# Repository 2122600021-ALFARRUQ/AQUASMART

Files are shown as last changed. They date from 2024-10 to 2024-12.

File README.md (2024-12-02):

flyer

# AQUA SMART
<div align="center">
    AQUA SMART Logo
</div>

## **Supported By:**  
🌟 **Dosen Pengampu:** Akhmad Hendriawan, S.T., M.T.  *(NIP: 197501272002121003)*  
🎓 **Mata Kuliah:** IOT dan Jaringan Sensor  
🎯 **Program Studi:** Sarjana Terapan Teknik Elektronika  
🏫 **Politeknik Elektronika Negeri Surabaya**  

# Daftar Isi

- [Deskripsi](#deskripsi)
- [Buku Panduan](#buku-panduan)
- [Komponen](#komponen)
   * [1. ESP32](#1-esp32)
   * [2. Sensor Ultrasonic](#2-sensor-ultrasonic)
   * [3. Flow Sensor](#3-flow-sensor)
   * [4. Adaptor 12V 2A](#4-adaptor-12v-2a)
   * [5. Solenoid Valve](#5-solenoid-valve)
   * [6. Modul Relay](#6-modul-relay)
- [Diagram Arsitektur](#diagram-arsitektur)
- [Tim Pengembang](#tim-pengembang)
- [Timeline Pengembangan](#timeline-pengembangan)
- [Rincian Pengeluaran Biaya](#rincian-pengeluaran-biaya)
- [Hardware](#hardware)
  * [1. Schematic Rangkaian](#1-schematic-rangkaian)
  * [2. Desain PCB](#2-desain-pcb)
  * [3. 3D Model PCB](#3-3d-model-pcb)
  * [4. Hasil 3D](4-hasil-3d)
- [Software](#software)
  * [1. Flowchart](#1-flowchart)
  * [2. Simulasi Wokwi](#2-simulasi-wokwi)
  * [3. Node-Red](#3-node-red)
  * [4. Sequence Diagram](#4-sequence-diagram)
  * [5. Class Diagram](#5-class-diagram)
- [Web APP](#web-app)
- [Dokumentasi](#dokumentasi)
  * [1. Video Percobaan Pengiriman Data dari ESP32 ke Broker MQTT](#1-video-percobaan-pengiriman-data-dari-esp32-ke-broker-mqtt)
  * [2. Video Simulasi Wokwi](#2-video-simulasi-wokwi)
  * [3. Video Simulasi Aplikasi](#3-video-simulasi-aplikasi)
    * [3.1 Video Simulasi Aplikasi Web](#31-video-simulasi-aplikasi-web)
    * [3.2 Video Simulasi Aplikasi Mobile](#32-video-simulasi-aplikasi-mobile)
  * [4. Video Pengujian Sensor Ultrasonik](#4-video-pengujian-sensor-ultrasonik)
  * [5. Video Pengujian Hardware](#5-video-pengujian-hardware)
  * [6. Video Penggunaan Alat (User)](#6-video-penggunaan-alat-user)
  * [7. Proses Pengerjaan](#7-proses-pengerjaan)
  * [8. Video Pengiklanan](#8-video-pengiklanan)
  * [9. Video Presentasi](#9-video-presentasi)

# Deskripsi
Sistem Monitoring Penggunaan Air Berbasis IoT ini dirancang untuk membantu rumah tangga dalam memantau penggunaan dan ketersediaan air secara real-time. Menggunakan ESP32 sebagai kontroler utama, sistem ini memanfaatkan sensor aliran air (Flow Sensor) untuk melacak jumlah air yang digunakan serta sensor ultrasonik untuk mengukur level air di dalam tangki penyimpanan. Data yang diperoleh akan dikirimkan ke platform cloud Adafruit IO melalui protokol MQTT, di mana pengguna dapat mengaksesnya melalui aplikasi ponsel atau website.

Dengan sistem ini, pengguna dapat mengelola air secara lebih efisien, mencegah kebocoran, dan menerima notifikasi dini ketika air di tangki hampir habis. Sistem juga dapat diperluas untuk memantau beberapa titik pengukuran berbeda di rumah, seperti dapur atau kamar mandi, dengan menambahkan modul tambahan.

# Buku Panduan
[Buku Panduan AquaSmart.pdf](https://github.com/2122600021-ALFARRUQ/AQUASMART/blob/3b80df1f71be8b21b987adbf3e9ceadbd6fab604/Buku%20Panduan%20AquaSmart.pdf)

# Komponen
## 1. ESP32
ESP32 adalah Mikrokontroler System on Chip (SoC) berbiaya rendah dari Espressif Systems, yang juga sebagai pengembang dari SoC ESP8266 yang terkenal dengan NodeMCU. ESP32 adalah penerus SoC ESP8266 dengan menggunakan Mikroprosesor Xtensa LX6 32-bit Tensilica dengan Wi-Fi dan Bluetooth yang terintegrasi.
ESP32 memiliki dua prosesor komputasi, satu prosesor untuk mengelola jaringan WiFi dan Bluetooth, serta satu prosesor lainnya untuk menjalankan aplikasi. Dilengkapi dengan memori RAM yang cukup besar untuk menyimpan data. Fitur yang berguna seperti TCP/IP, HTTP, dan FTP.
Pada proyek ini ESP32 berfungsi sebagai pusat pengendali yang mengumpulkan data dari sensor dan mengirimkannya ke sistem monitoring.

## 2. Sensor Ultrasonic
Sensor ultrasonik merupakan sensor yang menggunakan gelombang ultrasonik. Gelombang ultrasonik yaitu gelombang yang umum digunakan untuk mendeteksi keberadaan suatu benda dengan memperkirakan jarak antara sensor dan benda tersebut. Sensor ini berfungsi untuk mengubah besaran fisis (bunyi) menjadi besaran listrik begitu pula sebaliknya. Gelombang ultrasonik memiliki frekuensi sebesar 20.000 Hz. Bunyi tersebut tidak dapat didengar oleh telinga manusia. Bunyi tersebut dapat didengar oleh hewan tertentu seperti anjing, kelelawar dan kucing. Bunyi gelombang ultrasonik dapat merambat melalui zat cair, padat dan gas. Benda cair merupakan media merambat yang paling baik untuk sensor ultrasonik jika dibandingkan dengan benda padat dan gas. 
Pada proyek ini sensor ultrasonic digunakan untuk mengukur ketinggian air dengan memantulkan gelombang suara ke permukaan air. 

## 3. Flow Sensor
Flow sensor merupakan sensor yang digunakan untuk mengukur aliran cairan seperti gas atau cairan. Flow sensor memanfaatkan sub sistem mekanik dan listrik untuk mengukur perubahan atribut fisik fluida dan menghitung alirannya. Mengukur atribut fisik tergantung pada atribut fluida. Fluida gas, cair dan non-newtonian memiliki perilaku satu sama lain yang sangat berbeda sehingga metode yang digunakan untuk mengukur alirannya juga harus berbeda. Flow sensor bisa dibagi menjadi dua jenis, yaitu contact sensor dan non-contact sensor. Flow contact sensor digunakan dalam aplikasi dimana cairan atau gas yang diukur diperkirakan tidak akan tersumbat di dalam pipa ketika bersentuhan dengan bagian sensor yang bergerak. Sedangkan flow non-contact sensor tidak memiliki bagian yang bergerak dan biasanya digunakan ketika cairan atau gas yang dipantau akan terkontaminasi maupun diubah secara fisik serta bersentuhan dengan bagian yang bergerak. 
Pada proyek ini flow sensor berfungsi untuk mengukur aliran air yang mengalir dalam pipa.

## 4. Adaptor 12V 2A
Adaptor 12V 2A adalah sebuah alat yang digunakan untuk mengubah sumber daya listrik dari AC (arus bolak-balik) ke DC (arus searah), dengan output 12 volt dan kemampuan untuk memberikan arus hingga 2 ampere. Adaptor ini sering digunakan untuk perangkat elektronik seperti router, CCTV, dan berbagai peralatan lainnya yang membutuhkan sumber daya 12V DC. Adaptor 12V 2A digunakan untuk menyediakan daya yang stabil dengan tegangan 12V dan arus 2A. Komponen seperti solenoid valve dan relay membutuhkan daya ini untuk beroperasi. Adaptor memastikan sistem mendapatkan tegangan yang diperlukan tanpa gangguan.

## 5. Solenoid Valve
Solenoid valve adalah katup yang dikendalikan oleh arus AC atau DC melalui coil/selenoida. Katup Solenoid adalah elemen control yang paling sering digunakan dalam sistem fluida. Seperti pada sistem pneumatic, sistem hidrolik atau sistem control mesin memerlukan elemen control otomatis. Katup ini bisa dikendalikan oleh ESP32 untuk membuka atau menutup aliran sesuai kebutuhan.
Solenoid valve akan beroperasi jika coil/kumparan menerima tegangan arus yang sesuai dengan tegangan operasi (kebanyakan tegangan kerja katup solenoid adalah 100/200 VAC dan sebagian besar tegangan operasi pada tegangan DC adalah 12/24 VDC). Dan sebuah pin akan tertarik akibat gaya magnet yang dihasilkan oleh kumparan solenoid. Dan saat pin sitarik ke atas, cairan akan mengalir dengan cepat dari rongga C ke bagian D. Oleh karena itu, tekanan di rongga C berkurang dan tekanan cairan yang masuk akan menaikkan diafragma. Biarkan katup utama terbuka dan cairan mengalir langsung dari A ke F.

## 6. Modul Relay
Modul relay Arduino adalah perangkat keras yang berfungsi untuk mengontrol perangkat listrik eksternal seperti motor, lampu dan peralatan rumah tangga lainnya menggunakan platform Arduino. Modul ini terdiri dari relay dan beberapa komponen pendukung lainnya yang terintegrasi dengan papan sirkuit terpadu (PCB). Sedangkan relay adalah saklar elektronik yang dapat dikontrol secara elektrik. Ketika relay diberikan sinyal listrik, kontaknya akan terbuka atau tertutup, sehingga memungkinkan arus listrik mengalir atau terputus. Pada umumnya, modul relay ini terhubung ke papan Arduino melalui pin digital.
Modul Relay memungkinkan ESP32 mengontrol perangkat tegangan tinggi dengan aman, seperti solenoid valve atau pompa air, melalui sinyal dari mikrokontroler.

# Diagram Arsitektur
<div align="center">
    Gambar
</div>

# Tim Pengembang
<div align="center">
    STRUKTUR AQUA SMART
</div>

# Timeline Pengembangan

| Minggu | Tugas | Tanggal |
|---|---|---|
| 1 | Perencanaan dan pengajuan proposal | 01-10-2024 s/d 07-10-2024 |
| 2 | Pengembangan hardware dan pemrograman ESP32 | 08-10-2024 s/d 14-10-2024 |
| 3 | Pengujian sistem IoT dan integrasi cloud | 15-10-2024 s/d 21-10-2024 |
| 4 | Finalisasi dan presentasi proyek | 22-10-2024 s/d 04-11-2024 |

# Rincian Pengeluaran Biaya

| Item | Jumlah | Harga Satuan (Rp) | Total (Rp) |
|---|---|---|---|
| ESP32 | 1 | 75,000 | 75,000 |
| Sensor Ultrasonic | 1 | 10,000 | 10,000 |
| Flow Sensor | 1 | 74,000 | 74,000 |
| Adaptor 12V 2A | 1 | 16,000 | 16,000 |
| Solenoid Valve | 1 | 65,000 | 65,000 |
| Modul Relay | 2 | 8,200 | 16,400 |
| Kabel-Kabel | 1 | 10,000 | 10,000 |
| Cetak 3D | 1 | 200,000 | 200,000 |
| **Total Biaya** | - | - | **466,400**|

# Hardware
## 1. SCHEMATIC RANGKAIAN
Berikut ini adalah hasil skematik rangkaian sistem monitoring air menggunakan software Kicad
<div align="center">
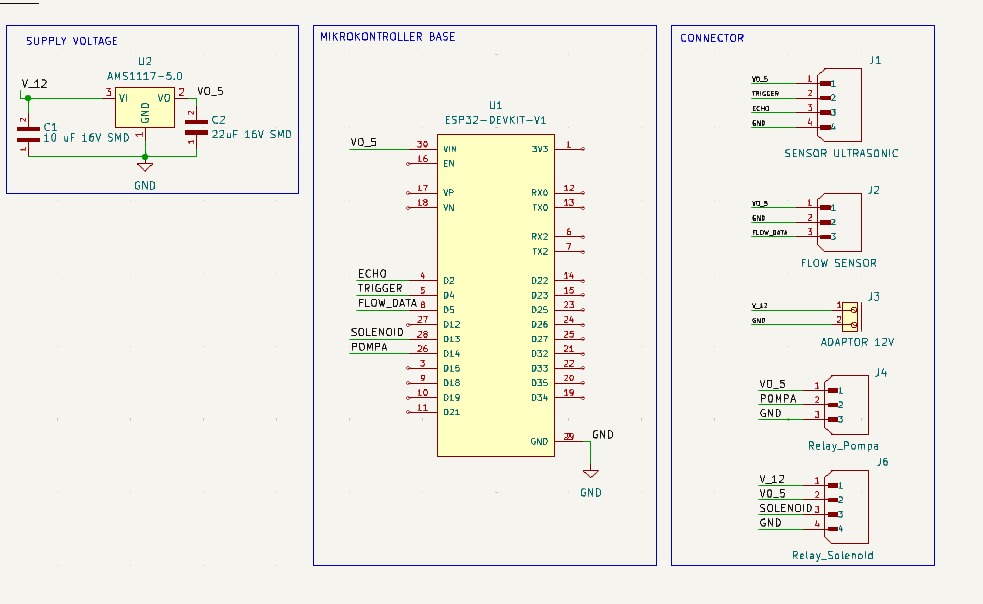
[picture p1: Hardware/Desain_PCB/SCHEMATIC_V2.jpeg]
SCHEMATIC RANGKAIAN
    
</div>

## 2. DESAIN PCB
Berikut ini adalah hasil layout rangkaian sistem monitoring air menggunakan software Kicad
<div align="center">
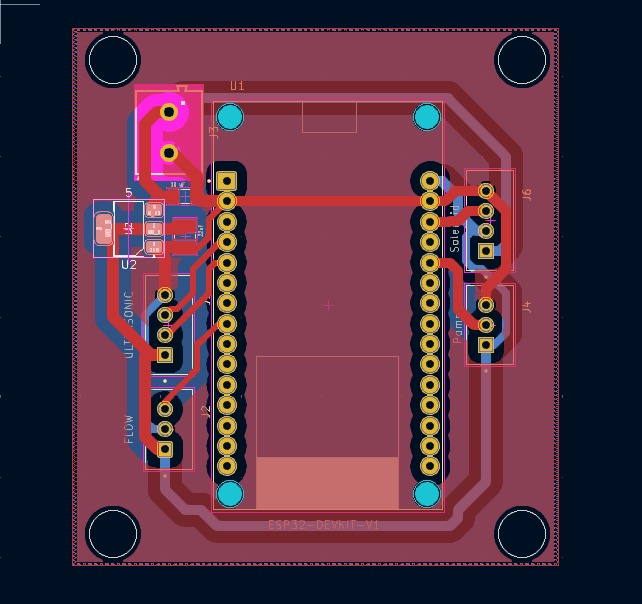
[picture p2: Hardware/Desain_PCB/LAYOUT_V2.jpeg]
DESAIN PCB
    
</div>

## 3. 3D MODEL PCB
Berikut ini adalah hasil 3D rangkaian sistem monitoring air menggunakan software Kicad
<div align="center">
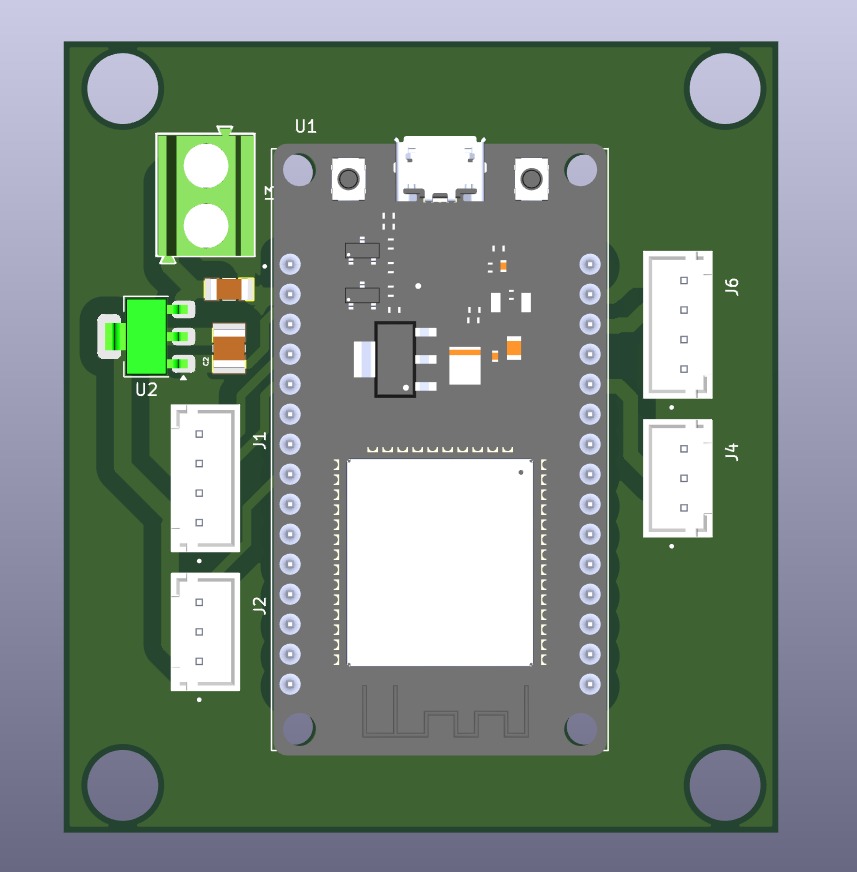
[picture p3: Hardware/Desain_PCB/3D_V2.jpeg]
3D MODEL PCB
    
</div>

Link Thingiverse : https://www.thingiverse.com/thing:6853870

Link PCB jadi : https://github.com/2122600021-ALFARRUQ/AQUASMART/tree/10eaccd06828d46e413301323a7a25bb22af950c/Hardware/Foto

## 4. Hasil 3D
<p align="center">
  
  
  
</p>
<p align="center">
  
  
</p>

# Software

## 1. FLOWCHART
<div align="center">
    
</div>
Flowchart diatas menggambarkan proses kerja sistem monitoring air menggunakan sensor ultrasonic dan rotary encoder. Proses dimulai dengan inisialisasi perangkat keras (setup). Sistem memeriksa apakah waktu tanpa aliran air melebihi ambang batas (threshold). Jika ya, nilai variabel encoderDelay disetel menjadi 1000 ms. Jika tidak, sistem menghitung laju aliran air (flow rate) menggunakan fungsi calculateMovingAverage(). Selanjutnya, sensor ultrasonic diaktifkan melalui fungsi ultrasonicTrigger(), dan persentase level air dihitung menggunakan fungsi ultrasonicCalculate(). Data hasil pengukuran berupa persentase level air dan flow rate ditampilkan pada LCD dan Serial Monitor. Pada sisi interrupt, ketika rotasi terdeteksi oleh rotary encoder, waktu saat ini disimpan dalam variabel timeNow, dan encoderDelay dihitung dari selisih timeNow dan timeLast. Nilai timeNow kemudian disimpan kembali ke timeLast untuk pembaruan data. Proses ini berulang secara kontinu untuk memastikan pengukuran berjalan real-time.

## 2. Simulasi Wokwi
<div align="center">
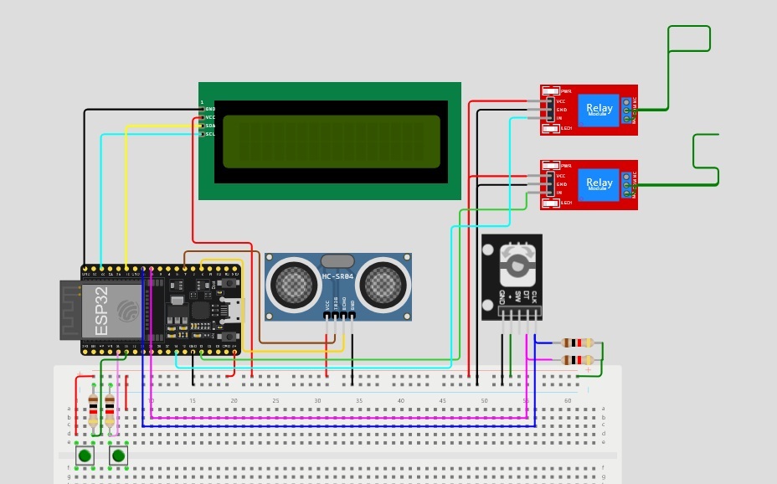
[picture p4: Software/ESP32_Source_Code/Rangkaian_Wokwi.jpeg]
Simulasi Wokwi
    
</div>
Simulasi pada gambar di atas menggunakan platform Wokwi bertujuan untuk memastikan bahwa rangkaian dapat berfungsi dengan baik sesuai desain, mulai dari membaca data sensor hingga menampilkan output pada LCD dan mengendalikan modul relay, sehingga meminimalkan potensi kesalahan sebelum implementasi pada perangkat keras sebenarnya

Link : https://wokwi.com/projects/411618765119428609

## 3. NODE-RED
<div align="center">
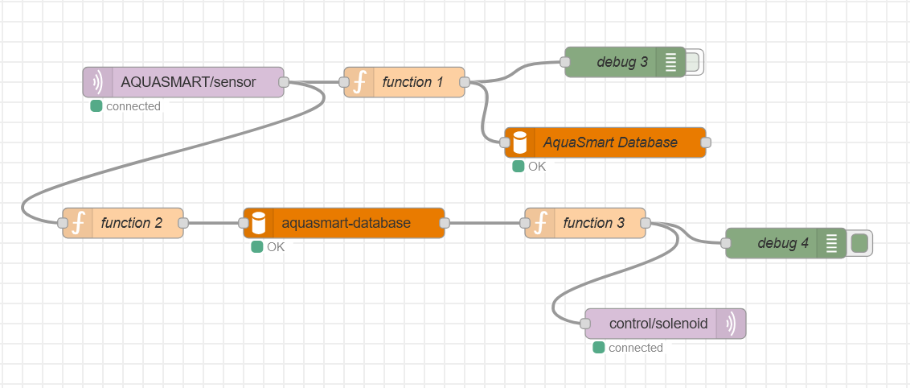
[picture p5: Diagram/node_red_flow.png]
    
</div>
Gambar di atas menunjukkan diagram alur Node-RED untuk sistem pengelolaan data berbasis IoT dengan topik AQUASMART. Dalam function 1 digunakan untuk mengolah data yang dikirimkan dari MQTT untuk diparsing agar bisa masuk kedalam database aquasmart. Terdapat percabangan dari Node AQUASMART/sensor yang menuju function 2. Data yang disimpan dapat diakses kembali melalui function ini yang mengarah ke node database. Hasil pemrosesan oleh function 3 dikirim ke control/solenoid untuk mengontrol katup solenoid.

## 4. SEQUENCE DIAGRAM
<div align="center">
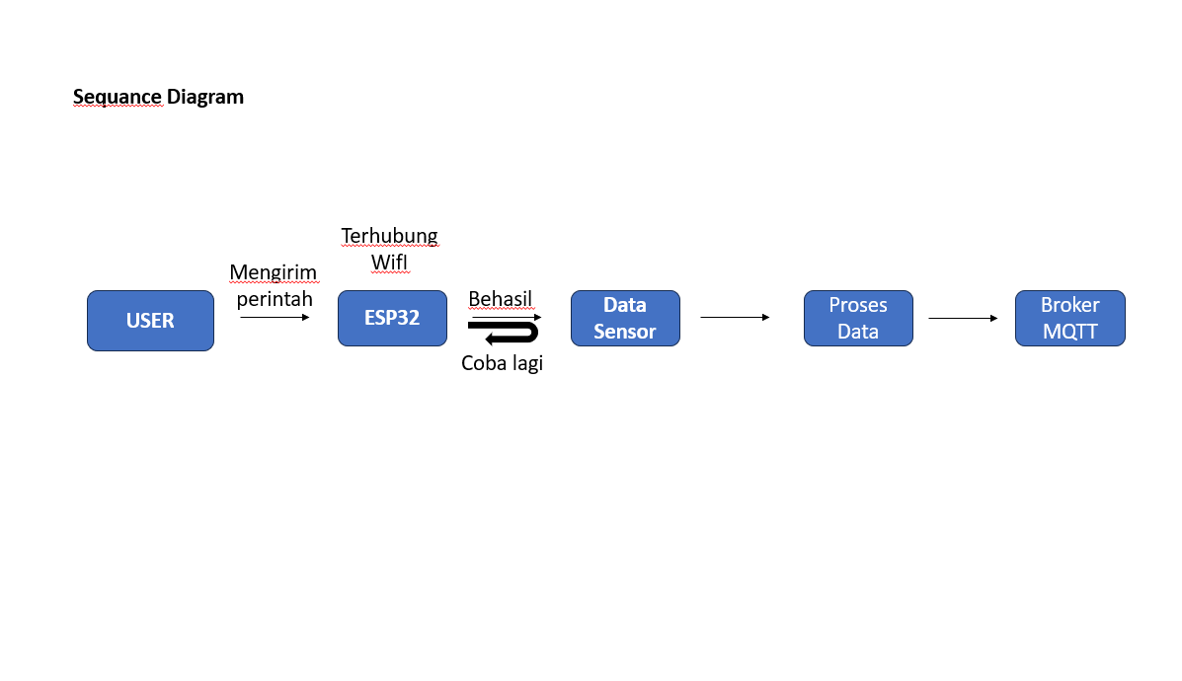
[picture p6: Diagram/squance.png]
SEQUENCE DIAGRAM
    
</div>

Sequence diagram pada gambar diatas menunjukkan alur komunikasi antara user, ESP32, sensor, dan broker MQTT dalam sistem IoT. Proses dimulai ketika user mengirimkan perintah ke ESP32 melalui jaringan Wi-Fi. ESP32 memverifikasi koneksi Wi-Fi hingga berhasil, namun jika gagal, sistem meminta user untuk mencoba lagi. Setelah terhubung, ESP32 membaca data dari sensor, lalu data tersebut diproses sebelum dikirim ke broker MQTT untuk diakses lebih lanjut. Diagram ini menunjukkan interaksi yang terorganisir untuk memastikan data dari sensor dapat diteruskan dengan akurat ke server atau aplikasi yang memanfaatkan MQTT sebagai protokol komunikasi.

## 5. CLASS DIAGRAM
<div align="center">
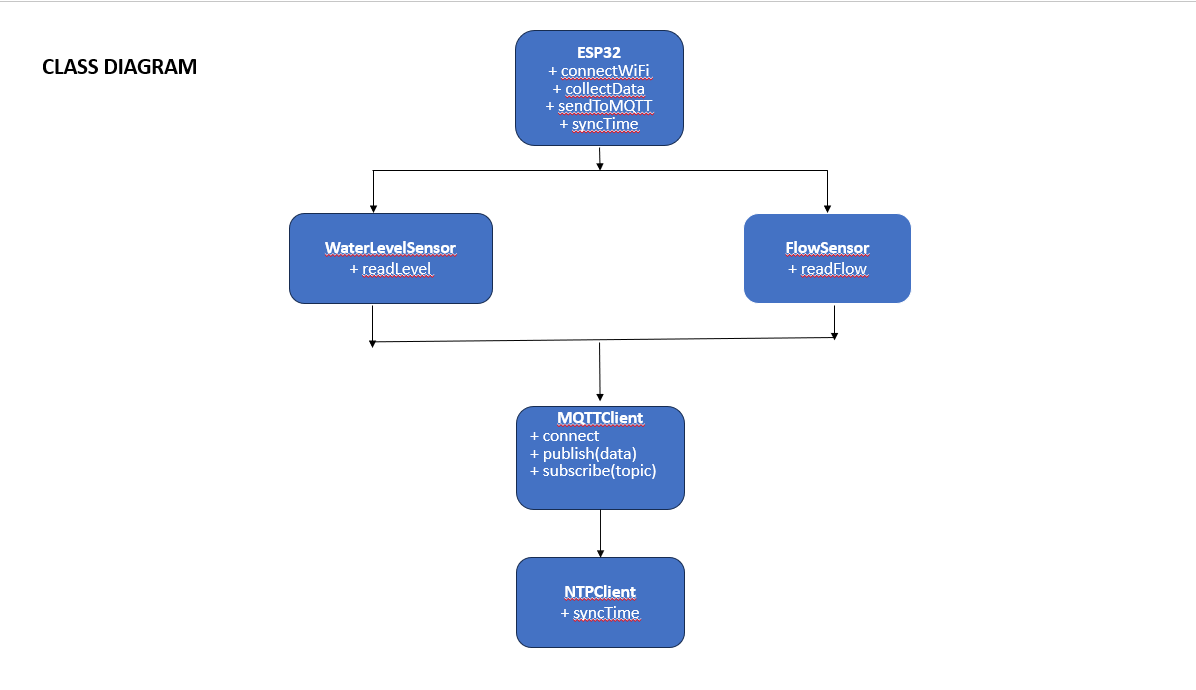
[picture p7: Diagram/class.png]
CLASS DIAGRAM
    
</div>

Gambar di atas menujukkan hubungan antar kelas dalam sistem berbasis ESP32 untuk pemantauan dan pengelolaan data. Kelas utama adalah ESP32, yang memiliki fungsi seperti connectWiFi (koneksi ke jaringan Wi-Fi), collectData (pengumpulan data dari sensor), sendToMQTT (mengirim data ke server MQTT), dan syncTime (sinkronisasi waktu menggunakan NTP). ESP32 berinteraksi dengan dua jenis sensor: WaterLevelSensor, yang memiliki fungsi readLevel untuk membaca ketinggian air, dan FlowSensor, yang menggunakan fungsi readFlow untuk mengukur aliran air. Data yang dikumpulkan kemudian dikirim ke MQTTClient, yang bertugas melakukan koneksi (connect), publikasi data (publish), dan langganan ke topik tertentu (subscribe). Selain itu, sinkronisasi waktu dilakukan dengan bantuan NTPClient melalui fungsi syncTime. Diagram ini menunjukkan arsitektur terintegrasi antara pengumpulan data sensor, komunikasi MQTT, dan sinkronisasi waktu.

# Web App
Link Web App Project Aquasmart dapat di lihat di sini : https://aquasmart-fdbackfue8hjdhgg.canadacentral-01.azurewebsites.net/

# Dokumentasi

## 1. Video Percobaan Pengiriman Data dari ESP32 ke Broker MQTT
https://github.com/user-attachments/assets/0b649f9e-3a0d-4be2-93d4-879152762dc5 
## 2. Video Simulasi Wokwi
https://github.com/user-attachments/assets/3788917b-d15c-42b3-9d15-79d57b5753b3 
## 3. Video Simulasi Aplikasi
### 3.1 Video Simulasi Aplikasi Web
https://github.com/user-attachments/assets/d782f18b-91e5-41b1-a5a1-bee070e43c8c
### 3.2 Video Simulasi Aplikasi Mobile
https://github.com/user-attachments/assets/036225ad-1f3f-4121-946e-6db940966c42
## 4. Video Pengujian Sensor Ultrasonik
https://github.com/user-attachments/assets/7d10899d-bf8c-4fc1-9f14-af5eacd0cc40 
## 5. Video Pengujian Hardware
https://github.com/user-attachments/assets/dedbf46f-3d43-4d81-ba96-16eca15a14ef
## 6. Video Penggunaan Alat (User)
https://youtu.be/zm1uCubxG-E
## 7. Proses Pengerjaan
<p align="center">
  
  
  
</p>
<p align="center">
  
  
</p>

## 8. Video Pengiklanan 
https://github.com/user-attachments/assets/52b6b247-8677-437f-991a-c6e8a309753d 
## 9. Video Presentasi
https://github.com/user-attachments/assets/3ab094f8-9b1d-4ff9-a2a7-7a724e087a73

slide presentasi dapat dilihat pada link berikut : https://github.com/2122600021-ALFARRUQ/AQUASMART/blob/2130463fc0ef71a656cedb03aadac50fb50dbc7b/IOT%20DAN%20JARINGAN%20_compressed.pdf

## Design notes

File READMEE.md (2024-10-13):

# AQUA SMART
AQUA SMART (1)

# WSN-PBL_IOT-Home-Water-Monitoring
Sistem Monitoring Penggunaan Air Berbasis IoT ini dirancang untuk membantu rumah tangga dalam memantau penggunaan dan ketersediaan air secara real-time. Menggunakan ESP32 sebagai kontroler utama, sistem ini memanfaatkan sensor aliran air (Flow Sensor) untuk melacak jumlah air yang digunakan serta sensor ultrasonik untuk mengukur level air di dalam tangki penyimpanan. Data yang diperoleh akan dikirimkan ke platform cloud Adafruit IO melalui protokol MQTT, di mana pengguna dapat mengaksesnya melalui aplikasi ponsel atau website.

Dengan sistem ini, pengguna dapat mengelola air secara lebih efisien, mencegah kebocoran, dan menerima notifikasi dini ketika air di tangki hampir habis. Sistem juga dapat diperluas untuk memantau beberapa titik pengukuran berbeda di rumah, seperti dapur atau kamar mandi, dengan menambahkan modul tambahan.

# Diagram Arsitektur
diagram arsitektur

# Tim Pengembang

| Nama | Nrp | Jobdesk |
|---|---|---|
| Al Farruq R. A. | 2122600021 | Project Manager |
| Farrel Juan M. | 2122600015 | Hardware Developer  |
| M. Rizqi Atmajaya | 2122600025 |  Project Tester |
| Owen Pratama S. |  2122600018 | Software Developer  |
| Aisyah |  2122600027 |  Data Analyst |
| Rheza Firmansyah | 2122600014 | UX/UI Designer |

# Timeline Pengembangan
| Minggu | Tugas | Tanggal |
|---|---|---|
| 1 | Perencanaan dan pengajuan proposal | 01-10-2024 s/d 07-10-2024 |
| 2 | Pengembangan hardware dan pemrograman ESP32 | 08-10-2024 s/d 14-10-2024 |
| 3 | Pengujian sistem IoT dan integrasi cloud | 15-10-2024 s/d 21-10-2024 |
| 4 | Finalisasi dan presentasi proyek | 22-10-2024 s/d 28-10-2024 |

# Estimasi Biaya

| Item | Jumlah | Harga Satuan (Rp) | Total (Rp) |
|---|---|---|---|
| ESP32 | 1 | 75,000 | 75,000 |
| Sensor Ultrasonic | 1 | 10,000 | 10,000 |
| Liquid Flow Sensor 3/4 Inchi SEA | 1 | 85,000 | 85,000 |
| Adaptor 5V 1A | 1 | 20,000 | 20,000 |
| Kabel-Kabel | 1 | 10,000 | 10,000 |
| Cetak 3D | 1 | 200,000 | 200,000 |
| **Total Biaya** | - | - | **400,000**|

# Hardware

# Software

# Spesifikasi Produk

# Petunjuk Penggunaan

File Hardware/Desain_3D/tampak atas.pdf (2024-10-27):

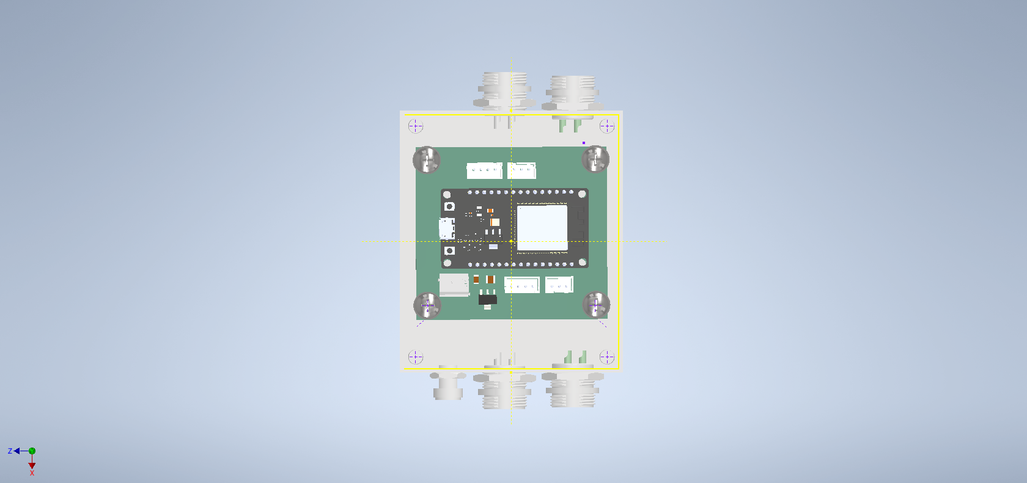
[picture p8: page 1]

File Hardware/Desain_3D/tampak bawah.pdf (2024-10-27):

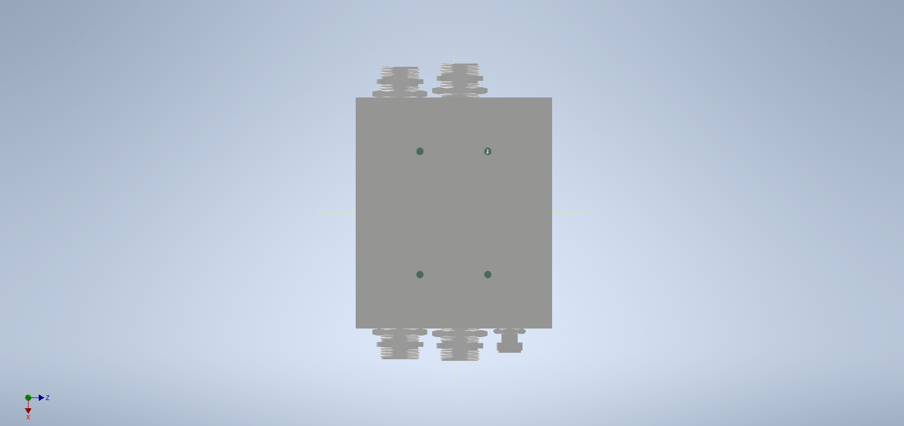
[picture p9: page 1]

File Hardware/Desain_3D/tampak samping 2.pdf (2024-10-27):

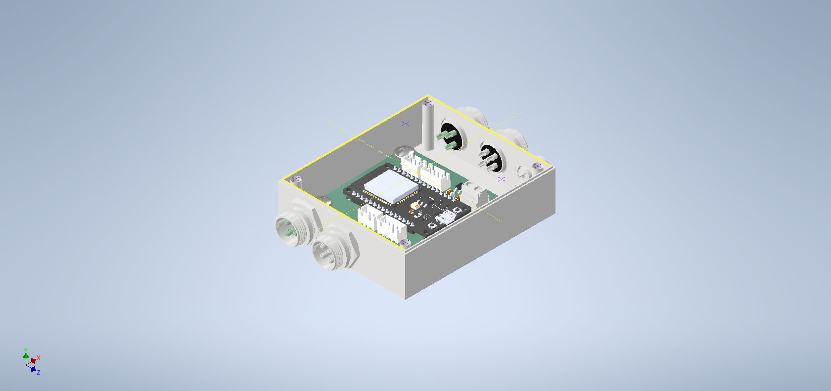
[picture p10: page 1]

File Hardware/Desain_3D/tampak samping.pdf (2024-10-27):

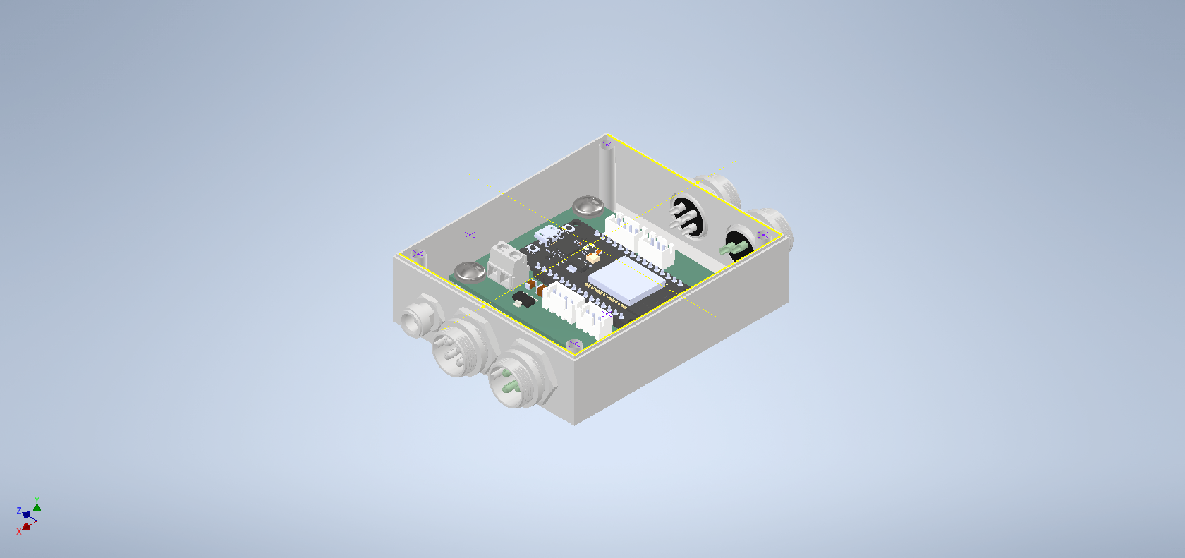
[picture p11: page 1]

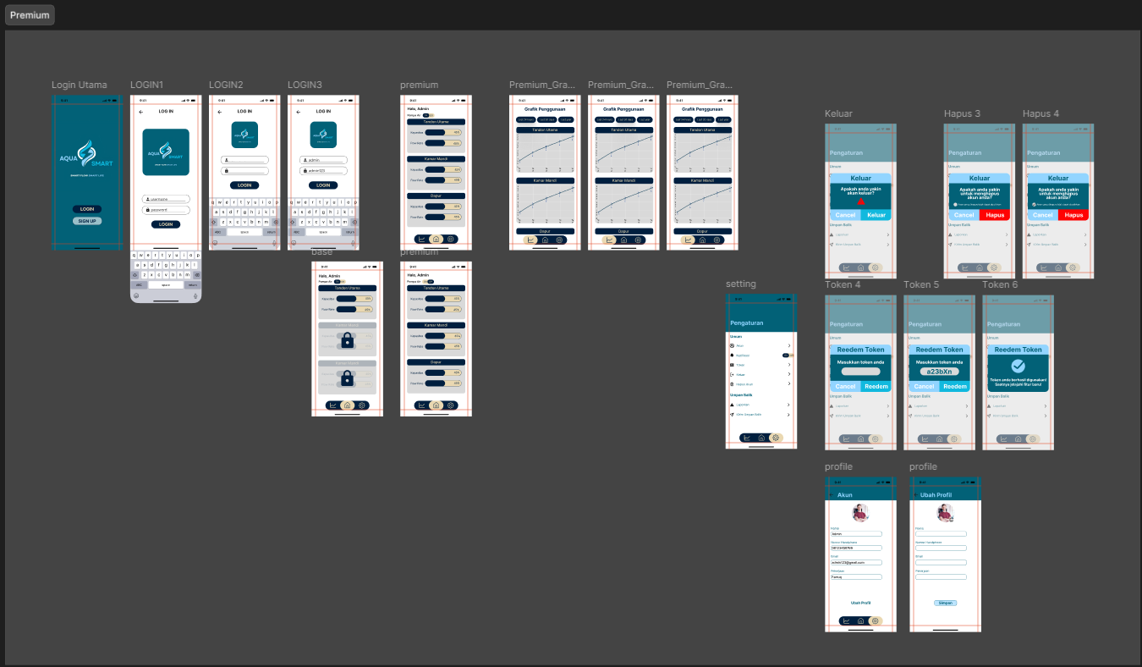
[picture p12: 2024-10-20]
Figma Design App/premiumbaru.png

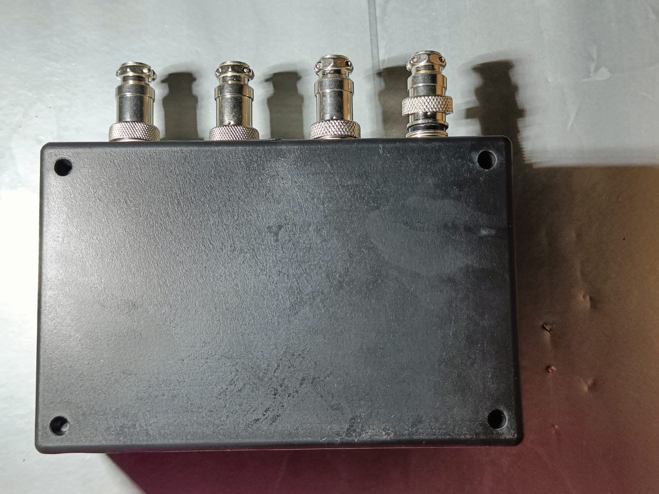
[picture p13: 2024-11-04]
Hardware/Final/Final (4).jpg

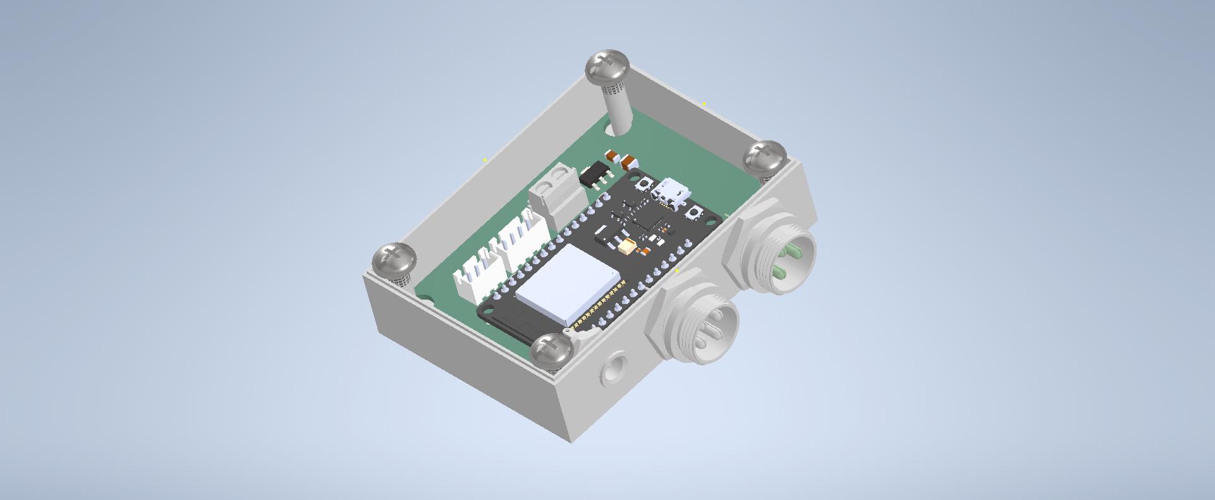
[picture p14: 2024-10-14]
Hardware/Desain_3D/tampak atas.jpg

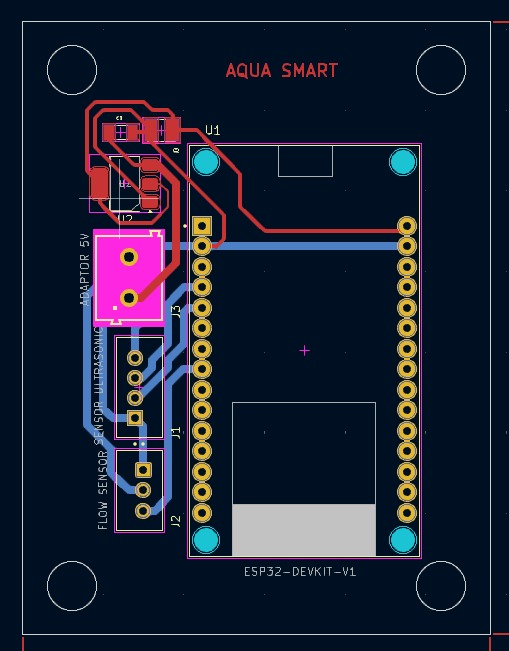
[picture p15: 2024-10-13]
Hardware/Desain_PCB/Desain_PCB.jpg

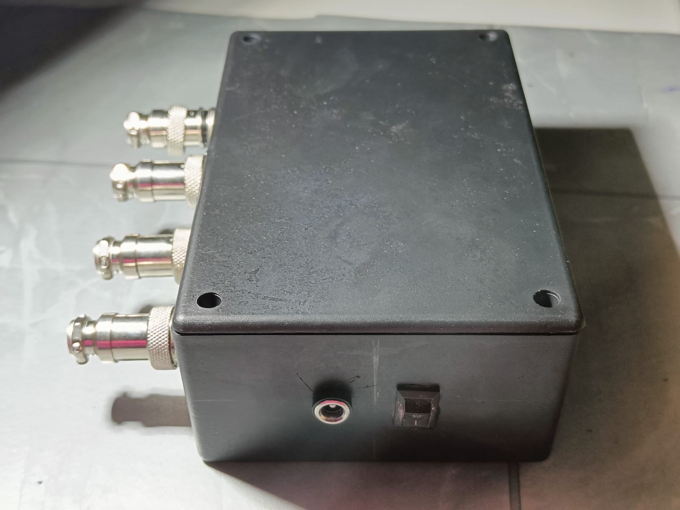
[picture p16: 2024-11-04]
Hardware/Final/Final (3).jpg

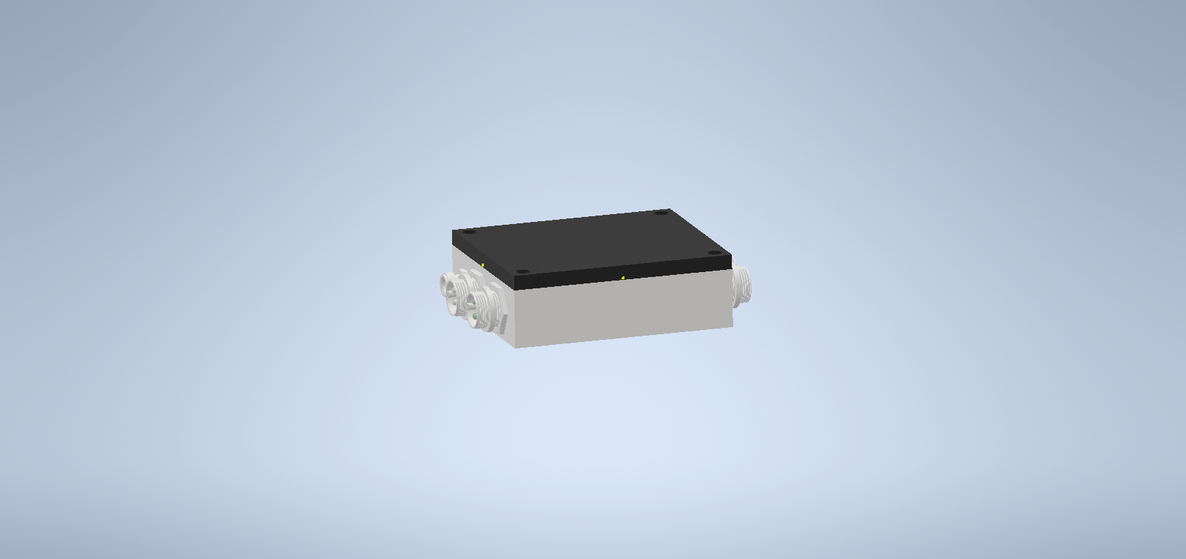
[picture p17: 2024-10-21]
Hardware/Desain_3D/progres2/aquasmart tutup.bmp

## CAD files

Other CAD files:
Hardware/Desain_3D/Assembly1.iam
Hardware/Desain_3D/Progres IoT 3.iam
Hardware/Desain_3D/progres2/ProjectIOT2.ipt

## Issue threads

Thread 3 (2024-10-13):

(M2) Desain PCB SHIELD Kicad

oreo240202, 2024-10-13:
Pembuatan Prototipe Awal Hardware
Tugas :
1.)  Desain PCB shield ESP selesai di KiCAD
2.)  Schematic dan layout PCB ter-upload ke GitHub

oreo240202, 2024-10-13:
[aquasmart_sch.pdf](https://github.com/user-attachments/files/17354783/aquasmart_sch.pdf)
[aquasmart-B_Cu.pdf](https://github.com/user-attachments/files/17354782/aquasmart-B_Cu.pdf)
[aquasmart-F_Cu.pdf](https://github.com/user-attachments/files/17354781/aquasmart-F_Cu.pdf)

oreo240202, 2024-10-13:
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

Closed 2024-10-13.

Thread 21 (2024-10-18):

(M3)Revisi Software

oreo240202, 2024-10-18:
Tambahkan Program untuk kontrol relay yang akan on/off secara otomatis berdasarkan bacaan dari sensor ultrasonic misalkan ketika ketinggian air mencapai 98% maka relay akan off sedangkan ketika 10%  relay akan aktif

Closed 2024-10-20.

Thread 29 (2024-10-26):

MQTT Ke Cloud/localhost

oreo240202, 2024-10-26:
Menggunakan mqtt untuk mengirim data dari esp32 (wokwi)  ke broker MQTT lalu ke cloud/local

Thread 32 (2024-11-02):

(M4) PCB + Casing

oreo240202, 2024-11-02:
PCB & CASING HARUS SUDAH JADI DALAM BENTUK FISIK REAL .. UPLOAD KE GITHUB HASIL JADINYA

oreo240202, 2024-11-03:
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
pcb sudah jadiii

Closed 2024-11-03.

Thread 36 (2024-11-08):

Pengujian Keakuratan Sensor Ultrasonik

2122600027-aisyah, 2024-11-08:
Pengujian keakuratan sensor ultrasonik dilakukan dengan menempatkan objek pada jarak yang telah diketahui di depan sensor dengan beberapa variasi jarak. Pengukuran diulang beberapa kali pada setiap jarak untuk memastikan konsistensi, dan hasilnya dibandingkan dengan jarak aktual untuk menghitung deviasi atau error

https://github.com/user-attachments/assets/7d10899d-bf8c-4fc1-9f14-af5eacd0cc40

Closed 2024-12-18.

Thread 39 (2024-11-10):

Percobaan pengiriman data dari Esp 32 ke Broker MQTT

2122600027-aisyah, 2024-11-10:
https://github.com/user-attachments/assets/0b649f9e-3a0d-4be2-93d4-879152762dc5

Closed 2024-12-18.

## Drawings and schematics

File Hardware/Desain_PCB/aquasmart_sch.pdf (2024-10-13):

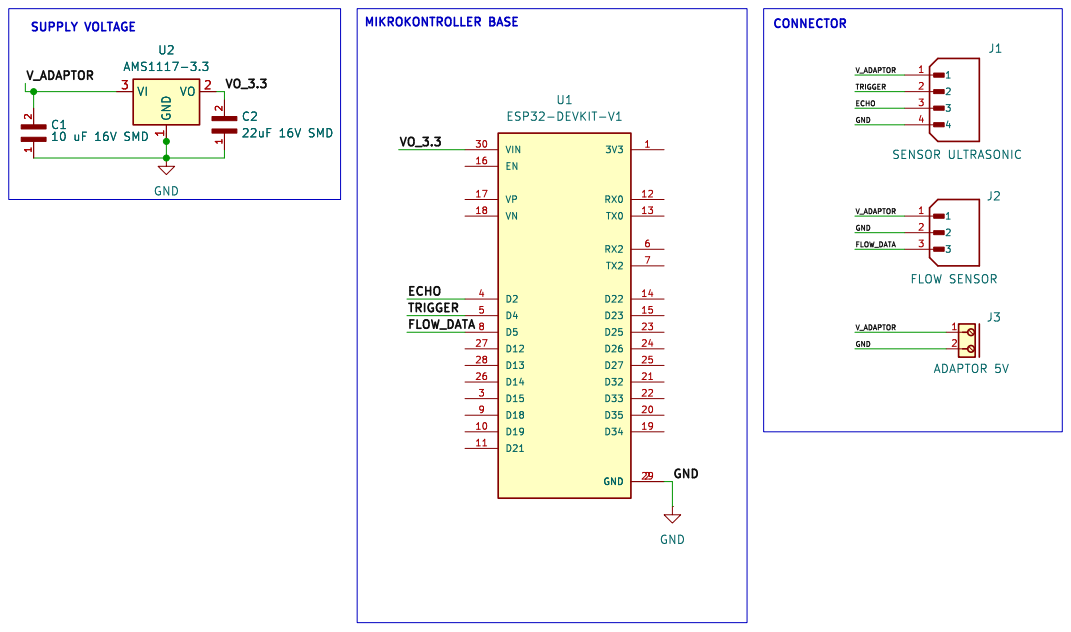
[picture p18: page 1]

Id: 1/1 Title: File: aquasmart.kicad_sch Sheet: /

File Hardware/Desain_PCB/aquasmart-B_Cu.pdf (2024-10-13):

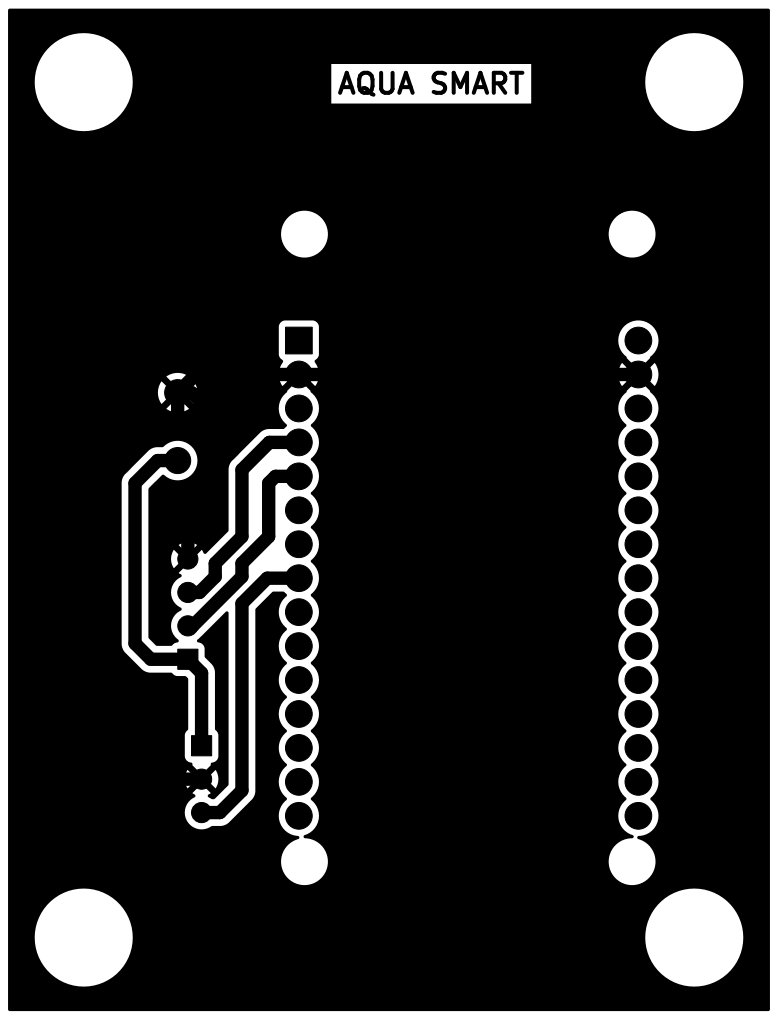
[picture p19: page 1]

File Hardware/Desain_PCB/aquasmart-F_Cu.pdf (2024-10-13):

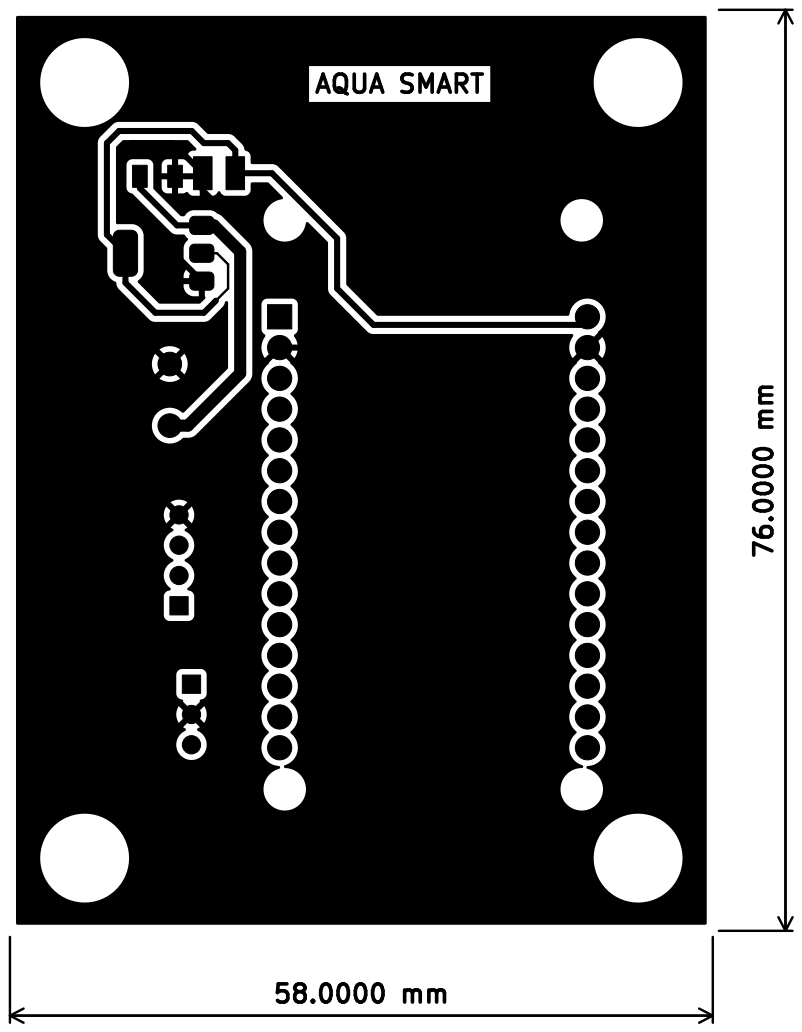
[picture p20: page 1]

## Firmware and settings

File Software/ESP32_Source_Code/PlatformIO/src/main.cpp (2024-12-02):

/*********
  Rui Santos & Sara Santos - Random Nerd Tutorials
  Complete instructions at https://RandomNerdTutorials.com/esp32-wi-fi-manager-asyncwebserver/
  Permission is hereby granted, free of charge, to any person obtaining a copy of this software and associated documentation files.
  The above copyright notice and this permission notice shall be included in all copies or substantial portions of the Software.
*********/
//catatan pin yang digunakan pada hardware seuai desain pcb :
// SENSOR ULTRASONIC : - PIN TRIGGER = 12
//                     - PIN ECHO = 14
// SENSOR FLOW       : - PIN DATA = D5  ((DISINI KARENA GAADA SENSOR FLOW MAKA MENGGUNAKAN PENGGANTI SIMULASI ROTARY ENKODER)) 
//                     - PIN DT = GPI018, CLK = GPIO19

#include <Arduino.h>

#include <Wire.h>
#include <LiquidCrystal_I2C.h>
#include <AiEsp32RotaryEncoder.h>
#include <PubSubClient.h>

#include <WiFi.h>
#include <ESPAsyncWebServer.h>
#include <AsyncTCP.h>
#include "LittleFS.h"

// Define Encoder Flow Sensor Constants
#define MAX_ENTRIES 5             // Keep track of the last 5 entries
#define VOLUME_PER_ROTATION 0.6   // 0.6 cm^3 per 18-degree rotation
#define ENCODER_DT 18             // Rotary Encoder DT Pin
#define ENCODER_CLK 19            // Rotary Encoder CLK Pin
#define NO_FLOW_THRESHOLD 500     // No-Flow time threshold (ms)

// MQTT Setup
const char* mqtt_server = "broker.mqtt.cool"; // Broker address
const int mqtt_port = 1883;

// MQTT topics
const char* topic_sensor = "AQUASMART/sensor";
const char* topic_flowRate = "sensor/flowRate";
const char* topic_percentage = "sensor/percentage";
const char* topic_solenoid = "sensor/solenoid";
const char* topic_pump = "sensor/pump";
const char* topic_solenoid_control = "control/solenoid"; // Control topic for solenoid

// WiFi and MQTT Client setup
WiFiClient espClient;
PubSubClient client(espClient);

// Create AsyncWebServer object on port 80
AsyncWebServer server(80);

// Search for parameter in HTTP POST request
const char* PARAM_INPUT_1 = "ssid";
const char* PARAM_INPUT_2 = "pass";
const char* PARAM_INPUT_3 = "ip";
const char* PARAM_INPUT_4 = "gateway";

//Variables to save values from HTML form
String ssid;
String pass;
String ip;
String gateway;

// File paths to save input values permanently
const char* ssidPath = "/ssid.txt";
const char* passPath = "/pass.txt";
const char* ipPath = "/ip.txt";
const char* gatewayPath = "/gateway.txt";

IPAddress localIP;
//IPAddress localIP(192, 168, 1, 200); // hardcoded

// Set your Gateway IP address
IPAddress localGateway;
//IPAddress localGateway(192, 168, 1, 1); //hardcoded
IPAddress subnet(255, 255, 0, 0);

// Timer variables
unsigned long previousMillis = 0;
const long interval = 10000;  // interval to wait for Wi-Fi connection (milliseconds)

// Pin assignments for Ultrasonic sensor
const int trigPin = 4;  // Ultrasonic Trigger Pin
const int echoPin = 2;  // Ultrasonic Echo Pin

// Flow Control Components pins
const int solenoidPin = 13;
const int pompaAirPin = 14;
const int solenoidOpenBtn = 34;
const int solenoidCloseBtn = 35;

// List to hold the last 5 delay times (in ms)
float delay_times[MAX_ENTRIES];
int count = 0;  // To track the number of entries added

// variables
long duration;      // Variable for Ultrasonic sensor duration
int distance;       // Variable for distance measured by the Ultrasonic sensor
int percentage;     // Variable for water level percentage
long timeNow;       // current time
long timeLast;      // previous recorded time (for flow rate calc)
int lastClk = HIGH; // previous encoder clk pin state
int newClk;         // current encoder clk pin state
int encoderDelay = 0;   // delay get from encoder
float flowRate;     // calculated flow-rate
int solenoidState = 1; // the state of the solenoid
int tresMin = 25, tresMax = 90; // Pump activation tank min and max values(in percent) // (activates at min, stops at max)
int setupMode = 0;
uint64_t timeAtReading = esp_timer_get_time();
uint64_t timeToPublish = 1000;

// Set LCD I2C address
LiquidCrystal_I2C lcd = LiquidCrystal_I2C(0x27, 16, 2);

// Function to convert distance to percentage (2 cm = 0%, 400 cm = 100%)
int convertToPercentage(int distance, int jarakMin, int jarakMax) {
  if (distance >= 400) return 0;
  if (distance <= 2) return 100;
  return map(distance, jarakMax, jarakMin, 0, 100);  // Mapping the value between 0 and 100%
}

float calculateFlowRate(float delay_time_ms) {
    // If delay exceeds threshold, return 0 (flow stopped)
    if (delay_time_ms > NO_FLOW_THRESHOLD) {
        return 0.0;  // Flow stopped
    }
    // Otherwise, calculate flow rate
    float delay_time_sec = delay_time_ms / 1000.0;  // Convert to seconds
    float flow_rate = VOLUME_PER_ROTATION / delay_time_sec;  // cm³/s
    return flow_rate;
}

// Function to calculate the moving average of flow rates
float calculateMovingAverage(float new_delay_time) {
    // If less than 5 values, add to the list directly
    if (count < MAX_ENTRIES) {
        delay_times[count] = new_delay_time;
        count++;
    } else {
        // Shift values to the left (remove the oldest value)
        for (int i = 0; i < MAX_ENTRIES - 1; i++) {
            delay_times[i] = delay_times[i + 1];
        }
        // Add the new delay time to the end
        delay_times[MAX_ENTRIES - 1] = new_delay_time;
    }

    // Calculate instantaneous flow rates for the last 5 delay times
    float total_flow_rate = 0;
    for (int i = 0; i < count; i++) {
        total_flow_rate += calculateFlowRate(delay_times[i]);
    }

    // Calculate the moving average flow rate
    float moving_average = total_flow_rate / count;
    return moving_average;
}

void ultrasonicSetup(){
  pinMode(trigPin, OUTPUT);
  pinMode(echoPin, INPUT);
}

void ultrasonicTrigger(){
  // Trigger the ultrasonic sensor
  digitalWrite(trigPin, LOW);
  delayMicroseconds(2);
  digitalWrite(trigPin, HIGH);
  delayMicroseconds(10);
  digitalWrite(trigPin, LOW);
}

void ultrasonicCalculate(){
  // Measure echo duration
  duration = pulseIn(echoPin, HIGH);

  // Calculate distance from duration (in cm)
  distance = duration * 0.0343 / 2;

  // Convert distance to percentage (2 cm = 0%, 400 cm = 100%)
  percentage = convertToPercentage(distance, 2, 400);
}

void ultrasonicDisplayDistance(){
  Serial.print("Distance: ");
  Serial.print(distance);
  Serial.println(" cm");
  lcd.setCursor(0, 1);
  lcd.print("Distance: ");
  lcd.print(distance);
}

void ultrasonicDisplayPercentage(){
  Serial.print("Percentage: ");
  Serial.print(percentage);
  Serial.println(" %");
  lcd.setCursor(0, 0);
  lcd.print("WtrLvl: ");
  lcd.print(percentage);
  lcd.print("%");
}

void readEncoder() {
  timeNow = millis();
  encoderDelay = 1 + timeNow - timeLast;
  timeLast = timeNow;
}

void encoderDisplayFlowRate(){
  Serial.print("Flow Rate: ");
  Serial.print(flowRate);
  Serial.println(" cm^3/s");
  lcd.setCursor(0, 1);
  lcd.print("flRate: ");
  lcd.print(flowRate);
  lcd.print(" cm3");
}

void flowconCheck(){
  if(percentage < tresMin){
    digitalWrite(pompaAirPin, HIGH);
  }
  else if(percentage >= tresMax){
    digitalWrite(pompaAirPin, LOW);
  }
}

void solenoidCheck(){
  if (digitalRead(solenoidOpenBtn) == LOW) {
    solenoidState = 1;
  }
  else if (digitalRead(solenoidCloseBtn) == LOW) {
    solenoidState = 0;
  }
}

void solenoidCState(){
  digitalWrite(solenoidPin, solenoidState);
}

// Callback function to handle incoming MQTT messages
void callback(char* topic, byte* payload, unsigned int length) {
  // Convert the payload to a string
  String message;
  for (unsigned int i = 0; i < length; i++) {
    message += (char)payload[i];
  }

  // Check if the message is for solenoid control
  if (String(topic) == topic_solenoid_control) {
    if (message == "1") {
      solenoidState = 1; // Turn ON solenoid
    } else if (message == "0") {
      solenoidState = 0; // Turn OFF solenoid
    }
    // Update solenoid pin state
    digitalWrite(solenoidPin, solenoidState);
    Serial.print("Solenoid State updated to: ");
    Serial.println(solenoidState);
  }
}

// MQTT reconnect function
void reconnect() {
  while (!client.connected()) {
    Serial.print("Attempting MQTT connection...");
    if (client.connect("ESP32Client")) {
      Serial.println("connected");
      client.subscribe(topic_solenoid_control);
    } else {
      Serial.print("failed, rc=");
      Serial.println(client.state());
      delay(2000);  // Wait and retry connection
    }
  }
}

// Initialize LittleFS
void initLittleFS() {
  if (!LittleFS.begin(true)) {
    Serial.println("An error has occurred while mounting LittleFS");
  }
  Serial.println("LittleFS mounted successfully");
}

// Read File from LittleFS
String readFile(fs::FS &fs, const char * path){
  Serial.printf("Reading file: %s\r\n", path);

  File file = fs.open(path);
  if(!file || file.isDirectory()){
    Serial.println("- failed to open file for reading");
    return String();
  }
  
  String fileContent;
  while(file.available()){
    fileContent = file.readStringUntil('\n');
    break;     
  }
  return fileContent;
}

// Write file to LittleFS
void writeFile(fs::FS &fs, const char * path, const char * message){
  Serial.printf("Writing file: %s\r\n", path);

  File file = fs.open(path, FILE_WRITE);
  if(!file){
    Serial.println("- failed to open file for writing");
    return;
  }
  if(file.print(message)){
    Serial.println("- file written");
  } else {
    Serial.println("- write failed");
  }
}

// Initialize WiFi
bool initWiFi() {
  if(ssid=="" || ip==""){
    Serial.println("Undefined SSID or IP address.");
    return false;
  }

  if(digitalRead(solenoidOpenBtn) == LOW || digitalRead(solenoidCloseBtn) == LOW){
    Serial.println("Wifi Setup Mode");
    return false;
  }

  WiFi.mode(WIFI_STA);
  localIP.fromString(ip.c_str());
  localGateway.fromString(gateway.c_str());

  
  //if (!WiFi.config(localIP, localGateway, subnet)){
  //  Serial.println("STA Failed to configure");
  //  return false;
  //}
  
  WiFi.begin(ssid.c_str(), pass.c_str());
  Serial.println("Connecting to WiFi...");

  unsigned long currentMillis = millis();
  previousMillis = currentMillis;

  while(WiFi.status() != WL_CONNECTED) {
    currentMillis = millis();
    if (currentMillis - previousMillis >= interval) {
      Serial.println("Failed to connect.");
      return false;
    }
  }

  Serial.println(WiFi.localIP());
  return true;
}


void setup() {
  // Serial port for debugging purposes
  Serial.begin(115200);

  initLittleFS();

  // lcd setup
  lcd.init();
  lcd.backlight();
  lcd.setCursor(0, 0);
  lcd.print("Kucing");

  // Set up ultrasonic sensor pins
  ultrasonicSetup();
  attachInterrupt(digitalPinToInterrupt(ENCODER_CLK), readEncoder, FALLING);
  timeNow = millis();

  // Rest of sensor setup
  ultrasonicSetup();
  pinMode(solenoidPin, OUTPUT);
  pinMode(pompaAirPin, OUTPUT);
  pinMode(solenoidOpenBtn, INPUT);
  pinMode(solenoidCloseBtn, INPUT);
  attachInterrupt(digitalPinToInterrupt(ENCODER_CLK), readEncoder, FALLING);
  timeNow = millis();
  
  // Load values saved in LittleFS
  ssid = readFile(LittleFS, ssidPath);
  pass = readFile(LittleFS, passPath);
  ip = readFile(LittleFS, ipPath);
  gateway = readFile (LittleFS, gatewayPath);
  Serial.println(ssid);
  Serial.println(pass);
  Serial.println(ip);
  Serial.println(gateway);

  if(initWiFi()) {
    Serial.println("Connected to WiFi");
    // Initialize MQTT
    client.setServer(mqtt_server, mqtt_port);
    client.setCallback(callback);
  }
  else {
    setupMode = 1;
    // Connect to Wi-Fi network with SSID and password
    Serial.println("Setting AP (Access Point)");
    // NULL sets an open Access Point
    WiFi.softAP("ESP-WIFI-MANAGER", NULL);

    IPAddress IP = WiFi.softAPIP();
    Serial.print("AP IP address: ");
    Serial.println(IP); 

    // Web Server Root URL
    server.on("/", HTTP_GET, [](AsyncWebServerRequest *request){
      request->send(LittleFS, "/wifimanager.html", "text/html");
    });
    
    server.serveStatic("/", LittleFS, "/");
    
    server.on("/", HTTP_POST, [](AsyncWebServerRequest *request) {
      int params = request->params();
      for(int i=0;i<params;i++){
        const AsyncWebParameter* p = request->getParam(i);
        if(p->isPost()){
          // HTTP POST ssid value
          if (p->name() == PARAM_INPUT_1) {
            ssid = p->value().c_str();
            Serial.print("SSID set to: ");
            Serial.println(ssid);
            // Write file to save value
            writeFile(LittleFS, ssidPath, ssid.c_str());
          }
          // HTTP POST pass value
          if (p->name() == PARAM_INPUT_2) {
            pass = p->value().c_str();
            Serial.print("Password set to: ");
            Serial.println(pass);
            // Write file to save value
            writeFile(LittleFS, passPath, pass.c_str());
          }
          // HTTP POST ip value
          if (p->name() == PARAM_INPUT_3) {
            ip = p->value().c_str();
            Serial.print("IP Address set to: ");
            Serial.println(ip);
            // Write file to save value
            writeFile(LittleFS, ipPath, ip.c_str());
          }
          // HTTP POST gateway value
          if (p->name() == PARAM_INPUT_4) {
            gateway = p->value().c_str();
            Serial.print("Gateway set to: ");
            Serial.println(gateway);
            // Write file to save value
            writeFile(LittleFS, gatewayPath, gateway.c_str());
          }
          //Serial.printf("POST[%s]: %s\n", p->name().c_str(), p->value().c_str());
        }
      }
      request->send(200, "text/plain", "Done. ESP will restart, connect to your router and go to IP address: " + ip);
      delay(3000);
      ESP.restart();
    });
    server.begin();
  }
}

void loop() {
  if (!client.connected() && setupMode == 0) {
    reconnect();
  }
  client.loop();
  if ((millis() - timeAtReading) >= timeToPublish && setupMode == 0){
    timeAtReading = millis();
    if (millis() - timeNow >= NO_FLOW_THRESHOLD) {
      encoderDelay = 1000;
    }
    // Calculate the moving average flow rate
    flowRate = calculateMovingAverage(encoderDelay);

    // Trigger ultrasonic and calculate distance, percentage
    ultrasonicTrigger();
    ultrasonicCalculate();
    flowconCheck();
    solenoidCheck();
    solenoidCState();

    // Display data on the Serial Monitor and LCD
    lcd.clear();
    ultrasonicDisplayPercentage();
    encoderDisplayFlowRate();

    // Convert `flowRate` and `percentage` to strings for publishing
    String solenoidStr = String(solenoidState);
    String pumpStr = String(digitalRead(pompaAirPin));
    String flowRateStr = String(flowRate);
    String percentageStr = String(percentage);
    String allData = flowRateStr + String(",") + percentageStr + String(",") + solenoidStr + String(",") + pumpStr;

    // Publish flowRate and percentage to MQTT topics
    //client.publish(topic_pump, pumpStr.c_str());
    //client.publish(topic_solenoid, solenoidStr.c_str());
    //client.publish(topic_flowRate, flowRateStr.c_str());
    //client.publish(topic_percentage, percentageStr.c_str());
    client.publish(topic_sensor, allData.c_str());
  }
  //else{
  //  Serial.println("Test");
  //}
}

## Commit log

2024-10-13 Create diisi pcb kicad
2024-10-13 Add Desain PCB Kicad
2024-10-13 Penambahan file Source Code untuk ESP32
2024-10-13 Rename Software/ESP32 Source Code/Link Wokwi.md to Software/Link Wokwi.md
    Penambahan link simulasi Wokwi
2024-10-13 Menambahkan Flowchart Program untuk ESP32
2024-10-13 Create Link Prototype
2024-10-13 Menambahkan Flowchart untuk Program ESP32
2024-10-13 Delete Software/ESP32 Source Code/Flowchart Program ESP32.svg
    Hapus Flowchart untuk perbaikan
2024-10-13 Upload ganti Flowchart Program ESP32
2024-10-13 Upload Ganti Flowchart Program
2024-10-13 Update and rename Link Prototype to Link Prototype.md
2024-10-13 Update Link Prototype.md
2024-10-14 Fixed invalid file paths
    [aquasmart.kicad_pcb, aquasmart.kicad_sch]
2024-10-14 Rename Link Prototype to Link Prototype
2024-10-14 Rename Link Prototype to Link_Prototype
2024-10-14 Rename Flowchart Program ESP32.svg to Flowchart Program ESP32.svg
2024-10-14 Rename Flowchart Program ESP32.svg to Flowchart_Program_ESP32.svg
2024-10-14 Upload foto schematic & design pcb
2024-10-14 menambahkan file case 3D
    [Assembly1.iam]
2024-10-14 foto case setiap sisi
2024-10-20 Update Project_AquaSmart.ino
    Menambahkan fungsi untuk mendeteksi level air dan menyalakan/mematikan Pompa Air secara otomatis. Juga ditambahkan fungsi untuk mengontrol Solenoid Valve untuk menyambung/putus aliran air.
2024-10-20 Delete Software/ESP32_Source_Code/Rangkaian_Wokwi.jpeg
    update rangkaian
2024-10-20 Delete Software/ESP32_Source_Code/Rangkaian_Wokwi.jpg
    salah penamaan
2024-10-20 Update README.md
    Mengupdate konsep diagram arsitektur dengan menambahkan solenoid dan pompa
2024-10-21 Menambahkan File Revisi Desain PCB
    menambahkan 2 header untuk relay solenoid dan pompa air
2024-10-21 update gambar Desain PCB pada README.md
    menambahkan gambar terbaru dari revisi gambar schematic, layout, 3d pcb
2024-10-21 Create progres 2
    penambahan mounting
2024-10-21 penambahan mounting
    penambahan 3 mounting dan mengubah ukuran box
    [ProjectIOT2.ipt]
2024-10-27 Add files via upload
    penambahan dudukan mur dan jarak konnector
    [Progres IoT 3.iam]
2024-11-03 menambahkan foto real pcb yang sudah jadi
    pcb sudah dicetak, dipasangi komponen dan disolder dengan baik....siap dipasangkan ke casingnya/ wadahnya
2024-11-03 Update Project_AquaSmart.ino
    Added MQTT Functionality:
    + Sending Flow Rate Value
    + Sending Water Level Value
    + Solenoid Control from Cloud
2024-11-04 Update Project_AquaSmart.ino
    + Sending Water Pump State
    + Sending Solenoid Valve State
    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
2024-11-08 Update README.md
    Penambahan Video Pengujian Sensor Ultrasonik
2024-11-24 Update program website
    + Menambahkan fungsi agar website dan database kompatibel dengan webhosting Microsoft Azure
    + Fix untuk fungsi tampilan kondisi (state) dari Solenoid dan Pompa Air
    + Menambahkan fungsi agar dapat melakukan kontrol Solenoid dari web
2024-11-24 Added NodeRed file
    + Node Red Flow ditambahkan fungsi untuk dapat mengirimkan data ke Hardware untuk menyalakan/mematikan Solenoid
2024-11-24 Menambahkan gambar Flow NodeRed Terbaru
2024-12-02 Update README.md
    1. menambahkan penjelasan deskriptif dari flowchart, simulasi wokwi, node red, sequence diagram, class diagram,
    2. menambahkan link video penggunaan alat dari sudut pandang user
2024-12-02 Menambahkan Source Code berbasis PlatformIO
    + Menambahkan fitur Wifi Manager
    > Meng-input kredensial Wifi pertama kali
    > Mengganti kredensial Wifi dengan menekan button di hardware
    > Mengganti kredensial Wifi jika tidak ada yang bisa di connect atau password/SSID salah
    + Menambahkan fungsi untuk bekerja dengan Wifi Manager
2024-12-02 Update README.md
    Penambahan link thingiverse dan pcb jadi
